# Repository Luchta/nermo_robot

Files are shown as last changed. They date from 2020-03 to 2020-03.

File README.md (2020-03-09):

# nermo_robot
 Hardware repository with all necessary files to build the NeRmo robot.

## DISCLAIMER

 This submission is to be used within the general terms of service of the Human Brain Project (HBP). In particular, users should not download the following code if they intend to make a military use of it.

## Repository Structure
* 3D Printing
	* STL_Files
	* Parts List
* Electronics
	* Eagle Files
	* Parts List
* Nermo User Manual.pdf
* README.md
* LICENSE

## License
[GPLv3](https://fsf.org/)

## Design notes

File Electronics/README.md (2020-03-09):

# nermo_robot
 Electronics Subfolder

## Custom PCBs

* LegSensorBoard
* RPiZWAdapterBoard
* ServoBoard
* Wire_Distr

## License
[GPLv3](https://fsf.org/)

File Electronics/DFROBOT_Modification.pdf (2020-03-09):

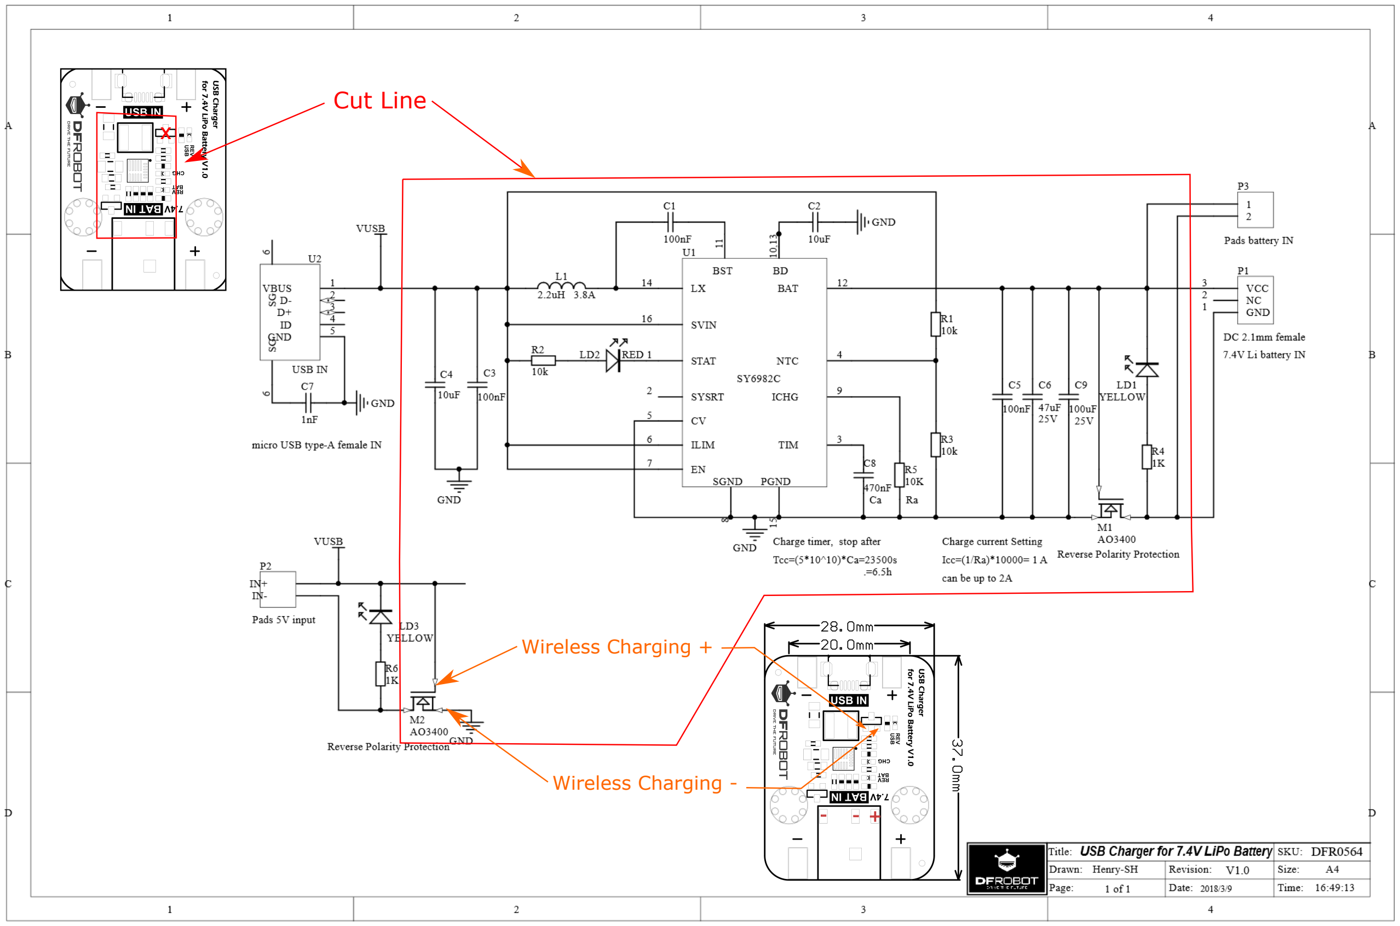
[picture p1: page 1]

### Cut Line

Wireless Charging +

Wireless Charging -

X

- - +

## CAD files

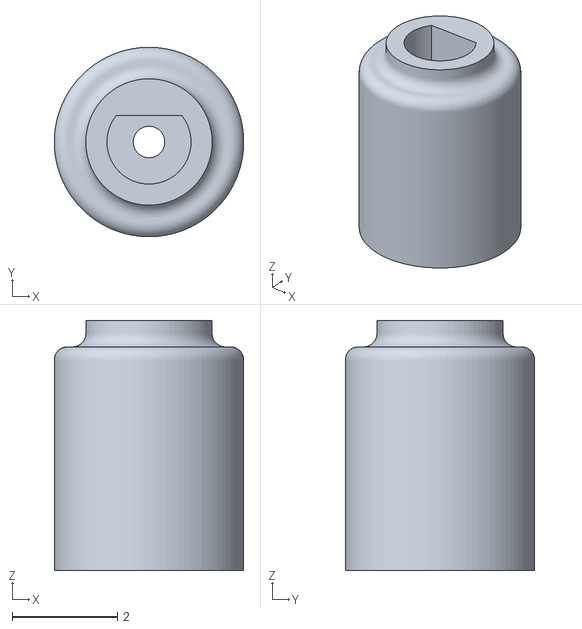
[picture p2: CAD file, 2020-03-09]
3D_Printing/Magnet_holder.stl
3.60 x 3.60 x 4.75

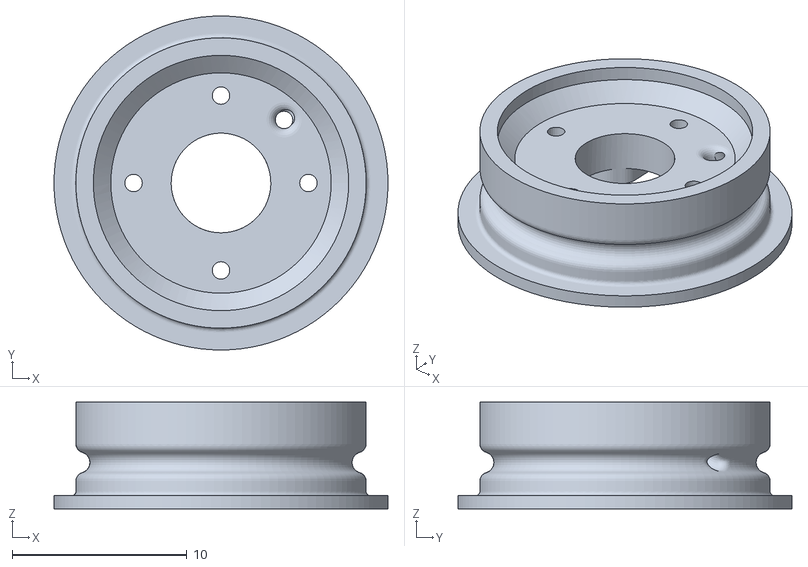
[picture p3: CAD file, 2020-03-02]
3D_Printing/Leg_Coil.stl
19.1 x 19.1 x 6.10

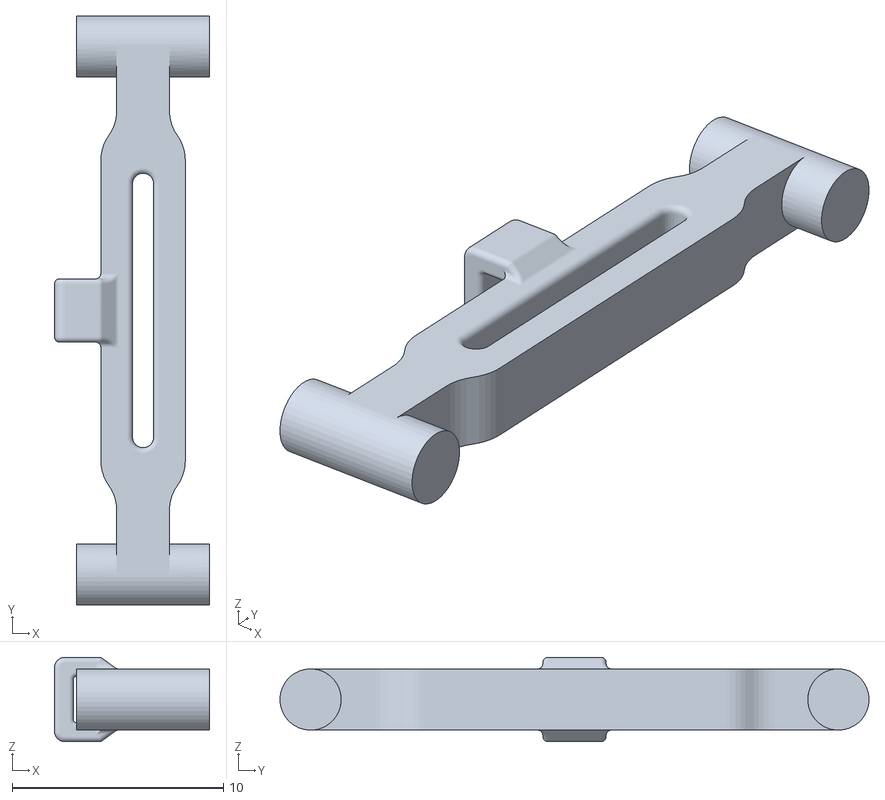
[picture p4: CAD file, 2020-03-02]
3D_Printing/Leg_Hind_Linkage.stl
7.35 x 27.9 x 4.00

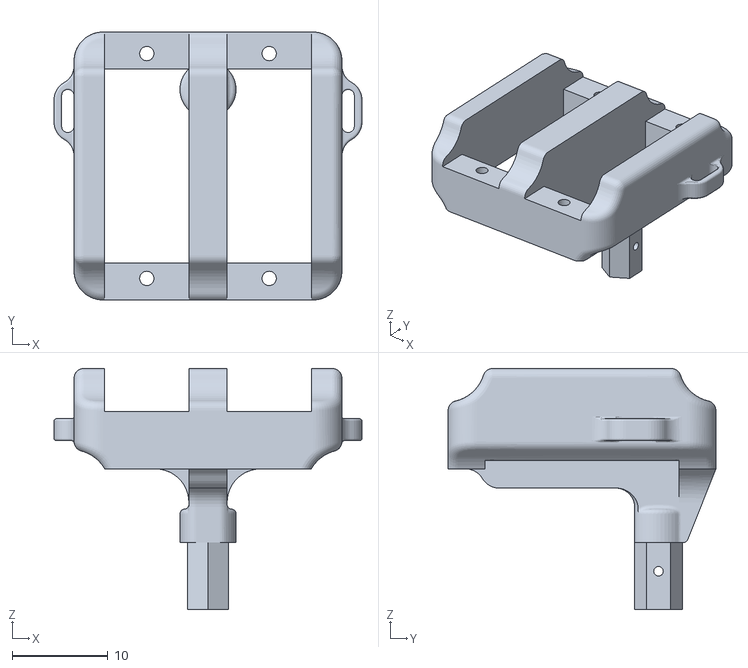
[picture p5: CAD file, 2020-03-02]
3D_Printing/Hip.stl
32.2 x 28.0 x 25.2

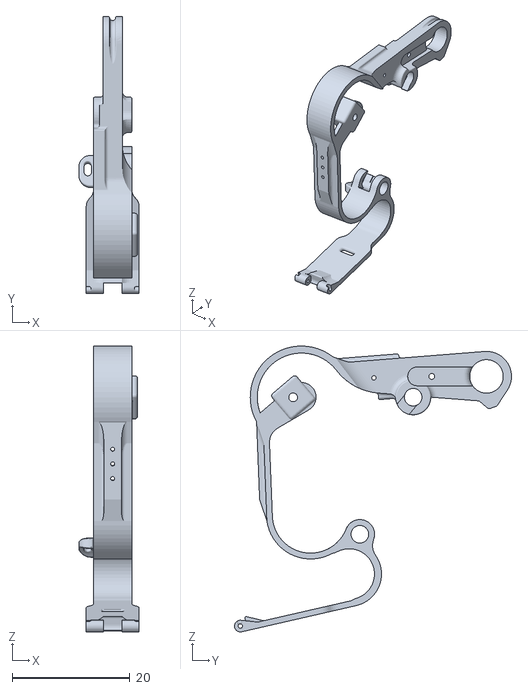
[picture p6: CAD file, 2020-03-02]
3D_Printing/Leg_Hind_Left.stl
10.2 x 47.1 x 48.6

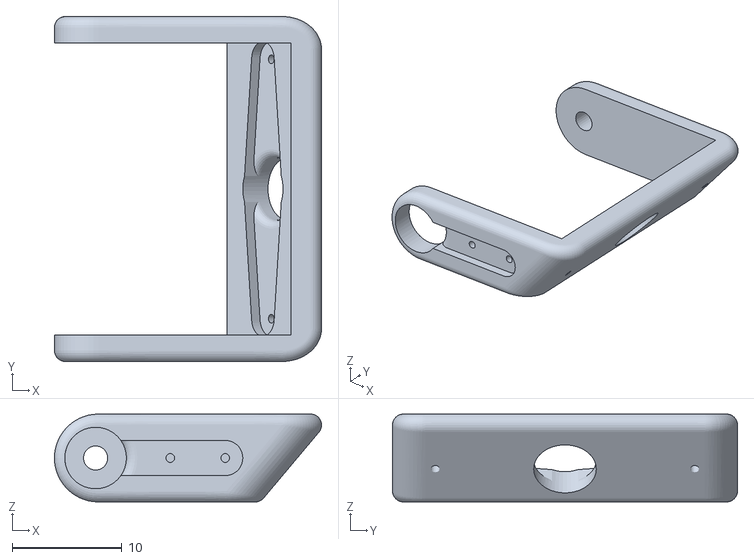
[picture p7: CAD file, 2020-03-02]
3D_Printing/Head_Neck.stl
24.3 x 31.4 x 8.00

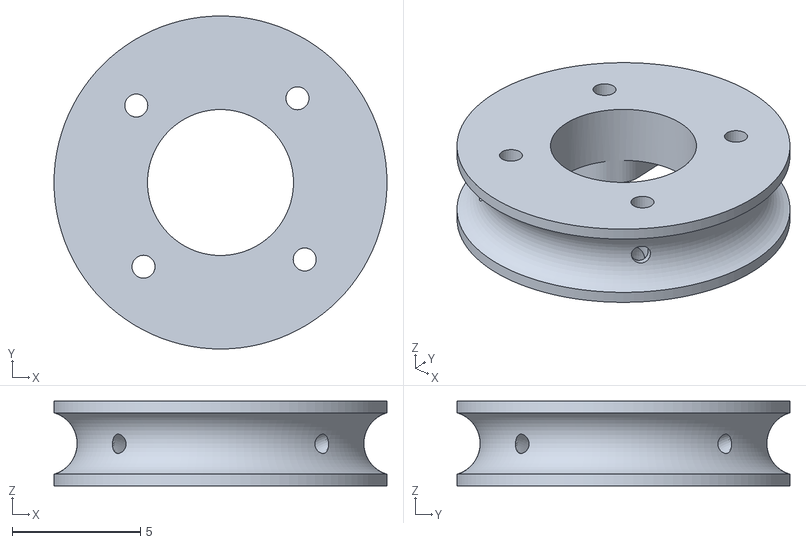
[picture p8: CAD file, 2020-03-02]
3D_Printing/Body_Coil.stl
13.0 x 13.0 x 3.30

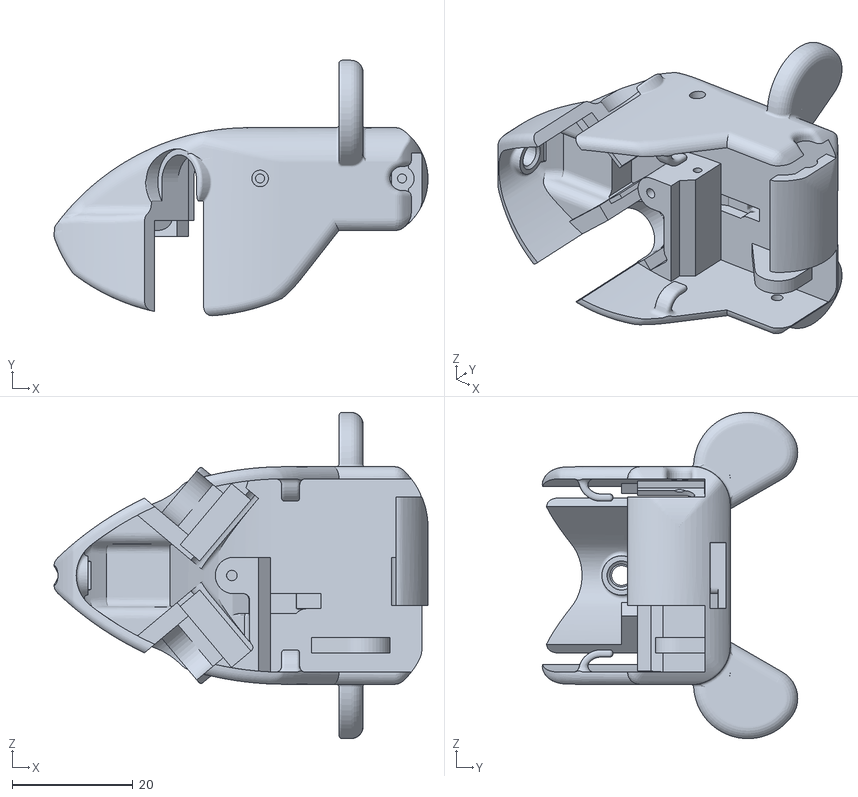
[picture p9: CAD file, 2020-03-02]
3D_Printing/Head.stl
61.9 x 42.3 x 54.0

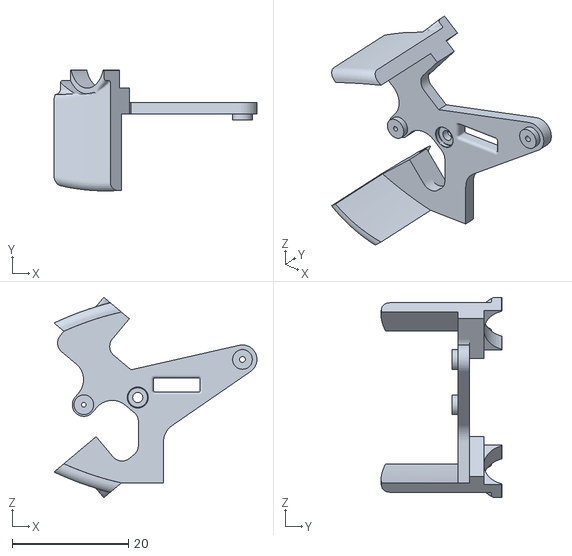
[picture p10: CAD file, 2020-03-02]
3D_Printing/Head_Camera_mount.stl
34.9 x 20.8 x 34.5

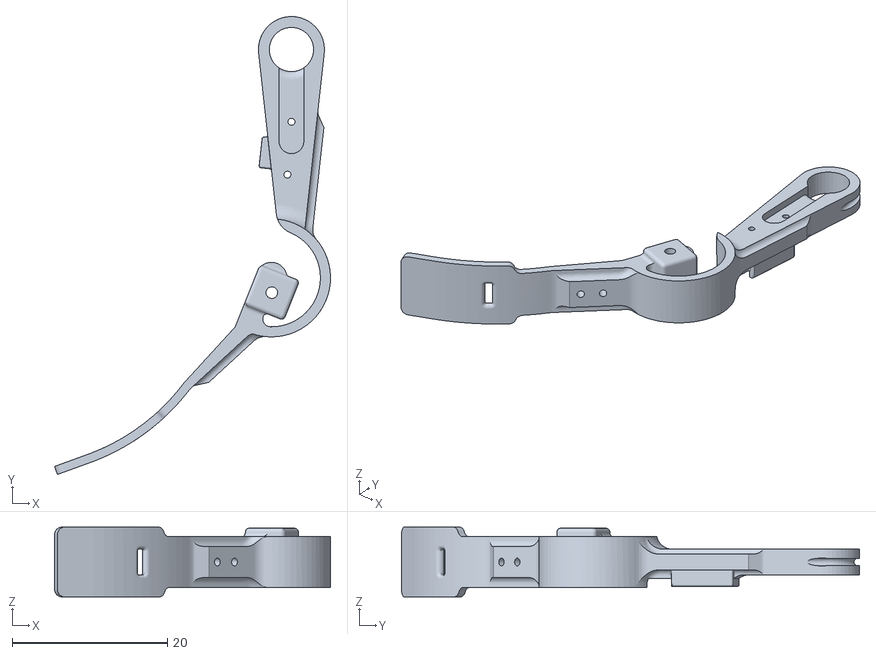
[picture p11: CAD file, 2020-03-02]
3D_Printing/Leg_Fore_Left.stl
35.5 x 58.9 x 9.00

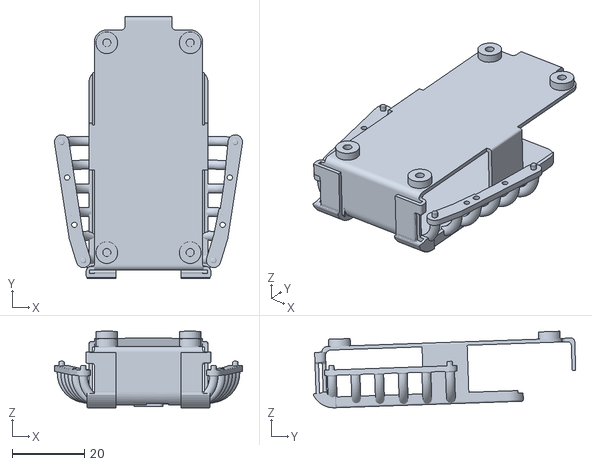
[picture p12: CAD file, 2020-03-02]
3D_Printing/Body_Solarplexus.stl
52.0 x 72.6 x 21.2

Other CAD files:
3D_Printing/Leg_Hind_Right.stl
3D_Printing/Leg_Fore_Right.stl

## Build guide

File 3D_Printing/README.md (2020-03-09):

# nermo_robot
 Hardware Subfolder
 
 All parts will have to be printed using Selective Laser Sintering (SLS) with Nylon (eos PA 2200 or similar).

## STLs to be 3D Printed

* Body
	* Body Coil (2 pcs)
	* Body Solarplexus (1 pcs)
	* Tail (1 pcs)
* Head
	* Head (1 pcs)
	* Head Camera mount (1 pcs)
	* Head Neck (1 pcs)
* Legs
	* Hip (4 pcs)
	* Leg Coil (4 pcs)
	* Leg Fore Left (1 pcs)
	* Leg Fore Right (1 pcs)
	* Leg Hind Left (1 pcs)
	* Leg Hind Right (1 pcs)
	* Leg Hind Linkage (2 pcs)
*Servos
	* Magnet_holder

## License
[GPLv3](https://fsf.org/)

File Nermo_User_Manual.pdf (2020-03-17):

# Nermo Robot

# User Manual

## Peer Lucas

### This Manual and the Robot resources are available free of charge from: https://github.com/Luchta/nermo robot (Hardware) https://github.com/Luchta/nermo code (Code) https://github.com/Luchta/nermo simulation (Simulation)

Abstract

### This manual serves to build, assamble and use the final version of the Neurorobotic mouse

robot, also called Nermo. This biomimetic robot is modular and low-cost; it was created to mimic the locomotion of a rodents, and has the size of a common rat (Rattus Norvegicus). The robot is untethered, easy to use and simple to produce; it thus can be used as a universal research platform. It is based on tendon-driven actuation, which enables the implementation of a compliant leg and body design and thus enables adaptive and dynamic walking motions. Small biomimetic robots can be useful for behavioural/social studies in combination with animals, or for investigating new, efficient types of locomotion for exploration systems. Combined with digital twins, they are a useful tool to reduce the reality gap between simulation and the real world.

Key words

Rodent; mouse; rat; robot; locomotion; biomimetic; tendon-driven actuation; Nermo.

i

# Table of Contents

1 Introduction | 1
2 Parts List | | 2
2.1 Custom Parts and Reusables | 3
3 Preparations | 4
3.1 Electronics | 4
3.1.1 | Servos | 4
3.1.2 | Spine Adapter Board | 4
3.1.3 | Leg Sensor Board | 5
3.1.4 | USB Hub | 5
3.1.5 | Wire Harness | 6
3.2 Reworking printing parts | 7
3.3 Coils | | 8
4 Components Assembly | 9
4.1 Hindleg | 10
4.2 Hindleg Module | 11
4.3 Foreleg | | 11
4.4 Foreleg Module | 12
4.5 Soldering Leg Modules | 12
4.6 Body Module | 13
4.7 Power and Compute Module | 14
4.8 Tail | | 16
4.9 Head | | 17
5 Whole Robot Assembly | 19
5.1 Stringing | 20
5.1.1 | Foreleg | 20
5.1.2 | Hindleg | 20
5.1.3 | Body Module | 21
5.1.4 | Tail Module | 22
5.2 Centre-line Assembly | 22
5.3 Wiring | | 23
6 First Setup | | 25
6.1 Connection Protocols | 25
6.2 Servo Programming | 25
6.3 Raspberry Pi setup | 26
6.4 Control software setup | 26
6.5 Leg setup | 26
7 Usage | | 27
7.1 Overview | 27
7.2 Charging | 27
7.3 Communication | 28
7.4 Control | | 29
References | | 30

ii

# List of Tables

Table 1 List of parts for the 13 modified servos. | 3

### Table 2 All additional parts needed from the original PowerHD HD-DSM44 Servo pack-

ages. | 3
Table 3 WIFI setup for the robot | 25
Table 4 Connection settings for the UART connections. | 25
Table 5 Servo IDs on the robot. | 28

# List of Figures

Fig. 1 Assembly of the custom Servos | 4
Fig. 2 Spine assembly board with all regulator and adapter boards. | 4
Fig. 3 Leg and pressure sensor prepared with wire. | 5
Fig. 4 Disassembly of the USB Hub. | 5
Fig. 5 Assembly of the USB Hub with the cameras. | 5
Fig. 6 Wire harness for connecting the 13 servos to the Spine Adapter Board. | 6

### Fig. 7 Detail view of the wire pathways in the body of the robot in red. The pathways

are symmetrical. Top: transparent body, Bottom: Solid body | 7

### Fig. 8 Detail view of the wire pathways in the tail of the robot in red. The pathways are

symmetrical. Top: transparent body, Bottom: Solid body | 7
Fig. 9 Assembly of the tendon coils. Top: Body coil, Bottom: Leg coil | 8
Fig. 10 NeRmo Module tree. | 9
Fig. 11 Exploded view of the Robot, without the left foreleg. | 9
Fig. 12 Assembly Process for the Hindlegs. | 10
Fig. 13 Soldering of the leg modules with schematic. | 12
Fig. 14 Assembly of the Body module. | 13
Fig. 15 Assembled Body module with transparent Body. | 13
Fig. 16 Assembly of the charging coil to the Power and Compute Module. | 14
Fig. 17 Assembly of the Power and Compute Module. | 15
Fig. 18 Connection of the charging board and the Spine Adapter board. | 15
Fig. 19 Assembly of the Tail Module | 16
Fig. 20 Head Module components | 17
Fig. 21 Assembly and schematic of the Head Sensors. | 18
Fig. 22 Assembly of the Head steps A-E. | 18
Fig. 23 Assembly of all sub modules to the complete Nermo Robot. | 19
Fig. 24 Stringing of the foreleg. | 20
Fig. 25 Stringing of the hindleg. | 20
Fig. 26 Stringing of the lateral tendon on the body module. | 21
Fig. 27 Stringing of the flex tendon on top of the body module. | 21
Fig. 28 Stringing of the foreleg. | 22
Fig. 29 Assembly of the centre line of the robot. | 22
Fig. 30 Attaching the Wiring harness to the leg modules | 23
Fig. 31 Attached Wire harnesses to the Spine, and both Leg sides. | 23
Fig. 32 Power and compute module connectors. | 24

### Fig. 33 Power and compute module attached to the body module with connected usb plug. 24

Fig. 34 programming cable to connect to the servos. | 25

### iii

Fig. 35 Initial setup position of the robot. | 26
Fig. 36 Electrical setup of the robot. | 27
Fig. 37 charging coil of the robot. | 28

iv

### 1. Introduction

The present report details the evolution of the so-called Neurorobotic Mouse robot, and presents the main features of its latest release. The development of that robot was initiated in 2018 [1] with the view to become a general-purpose research robot for roboticists and neuroscientists alike. Over the last two years, four main successive versions [2] were built before finally ob-taining the final version described herein. The minimal set of features for such a robot to be

### useful to all intended users [2] are:

- Flexible and functional backbones.
- Biologically relevant limbs with a small number of parts (for ease for build).
- A functional tail (for facilitating balance and locomotion).

### - A sensory system sufficient to provide the robot with capabilities for autonomous navi-

gation and decision-making.

- Tendon-driven actuation that mimics the biological musculoskeletal system of a rodent.

Additionally, the perquisites for this project where to create a low-cost and modular robot, in order to facilitate uptake of the device in the research community. These features were already realized with the last version of this robot [2]. The Final version presented herein features multiple improvements over previous iterations, especially ease of assembly and robustness to allow for a wider user group. Additionally, we created a digital twin of the robot (i.e. a simulated model, reproducing the characteristics of the real one with as much fidelity as possible) within the Neurorobotics Platform (NRP).

### 2. Parts List

Category | Item | Description | Quantity
Electronics
| Raspberry Pi Zero W | Main Computer | 1
| Micro SD memory card | Storage for RasPi | 1
| Akku-Pack, Li-Polymer, 7,4 V
| 1000 mAh, 2, 25 C | Battery | 1
| Nose Touch Button | Nose Touch Button | 1
| 1.0mm 1.0 SH Micro JST
| with 15cm Wire | Cable to connect Servos | 17
| Cable to connect leg sensor PCB | Cable to connect leg sensor
| | PCB | 4
| 0-200g Thin Film Pressure Sensor | Foot Pressure Sensor | 4
| Micro USB Hub | USB Hub for Cameras | 1
| U1-MWD | Camera in Head | 2
| Modified PowerHD HD-DSM44 | Motors | 13
| Spine Adapter Board | Power and Motor control | 2
| Leg Sensor Board | Angle and Pressure sensor | 2
| 4 Hole Wiring Board | Wiring Harness | 2
| 5 Hole Wiring Board | Wiring Harness | 1
Mechanics
| M2x8 | Head Tilt Axis | 1
| M2x6 | Camera holder | 1
| M2x14 | Tail Mount | 1
| M2 Stop-nut | Tail Mount | 1
| M1x4 | Leg-Wire Fixes | 20
| M1*3 | Leg-Wire Fixes | 10
| M1x8 | Hip Fix | 8
| Magnet 4x4x4 mm | Leg Sensor Magnet | 8
| M2,5*6,5 | Distance holder for RasPi | 4
| India rubber tape
| self-adhesive | Feet covering | 1
| Perlon thread
| ø0,3 mm length 50 m | Tendons | 1
3D Prints | | | 22
| Body | Main Body of the Mouse | 1
| Body Coil | Small Coils for Tendons | 2
| Body Solarplexus | Holder for Battery and Raspi | 1
| Head | Robot Head | 1
| Head Camera mount | mount for all head components | 1
| Head Neck | Connection Head-Body | 1
| Hip | Servo Mount for all Legs | 4
| Leg Coil | Coils for Leg tendons | 4
| Leg Fore Left | Left Foreleg | 1
| Leg Fore Right | Right Foreleg | 1
| Leg Hind Left | Left Hindleg | 1
| Leg Hind Right | Right Hindleg | 1
| Leg Hind Linkage | Linkage for Hindlegs | 2
| Tail | Tail | 1

### 2.1 Custom Parts and Reusables

The Servo motors for this robot will have to be modified according to the servo modification manual in this repository. The parts needed for the modification are the following Table 1.

Item | Description | Quantity
PowerHD HD-DSM44 | Servo | 13
M1x12 | Attach servo PCB | 26
Custom servo PCB | New control board | 13
Magnet 2x2x2 mm | Magnet for Hall sensor | 13
Servo magnet holder | 3D printed magnet holder | 13

Table 1. List of parts for the 13 modified servos.

Additionally. some parts come with the original PowerHD HD-DSM44 servos, that will be used in the build as listed in Table 2.

Item | Description | Quantity
Servo Horn Cross | All Coils | 6
Servo Horn Lever | Legs and Neck | 5
Servo Horn Bar | Neck and Tail | 2
Servo Horn Screw | Mount all Horns 1.6x3 | 13
Attachment Screw | Mount all Servos wood screw 1.6x6 (DIN 7981) | 26

Table 2. All additional parts needed from the original PowerHD HD-DSM44 Servo packages.

### 3. Preparations

There are some preparations to be taken before the robot can be assembled.

### 3.1 Electronics

Additionally to the Servo PCBs there are two types of PCBs that will have to be assembled before the robot can be build. Those are the Spine Adapter Board and the Leg Sensor Board. For both boards the eagle files and assembly manuals can be found in the folder ”/Electronics/Eagle/”

### 3.1.1 Servos

Before starting with the Robot’s assembly, make sure that you have 13 assembled servos. The Manual on how to assemble the custom servos can be found in the same directory as this manual (Servo Assembly.pdf) Figure 1 shows a overview of the assembly process.

Fig. 1. Assembly of the custom Servos

### 3.1.2 Spine Adapter Board

The Spine Adapter board goes on top of the Raspberry Pi Zero and handles communication and power distribution in the robot. Additionally to the PCB there are some off the shelf parts, that are added to the board as shown in Figure 2.

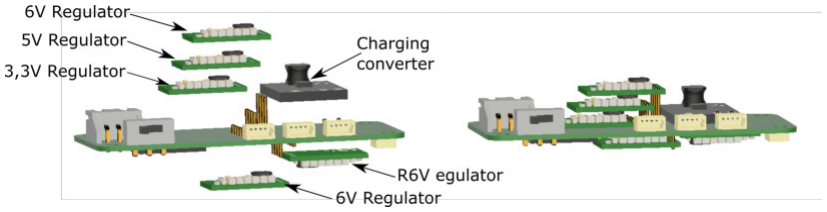
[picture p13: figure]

Fig. 2. Spine assembly board with all regulator and adapter boards.

### 3.1.3 Leg Sensor Board

The leg sensor boards have a hall sensor to measure the knee/elbow angles as well as a ADC to measure the ground pressure with the pressure sensors. To have less work later on you can solder wires already to the according pads (Figure 3).

Fig. 3. Leg and pressure sensor prepared with wire.

### 3.1.4 USB Hub

To address the cameras in the Head, we used a simple USB-Hub. This Hub can be bought from Amazon or anywhere else. We only need the core pcb as shown in Figure 4. After Disassembly, the cameras and a USB cable can be soldered to the USB Hub as shown in Figure 5.

Fig. 4. Disassembly of the USB Hub.

Fig. 5. Assembly of the USB Hub with the cameras.

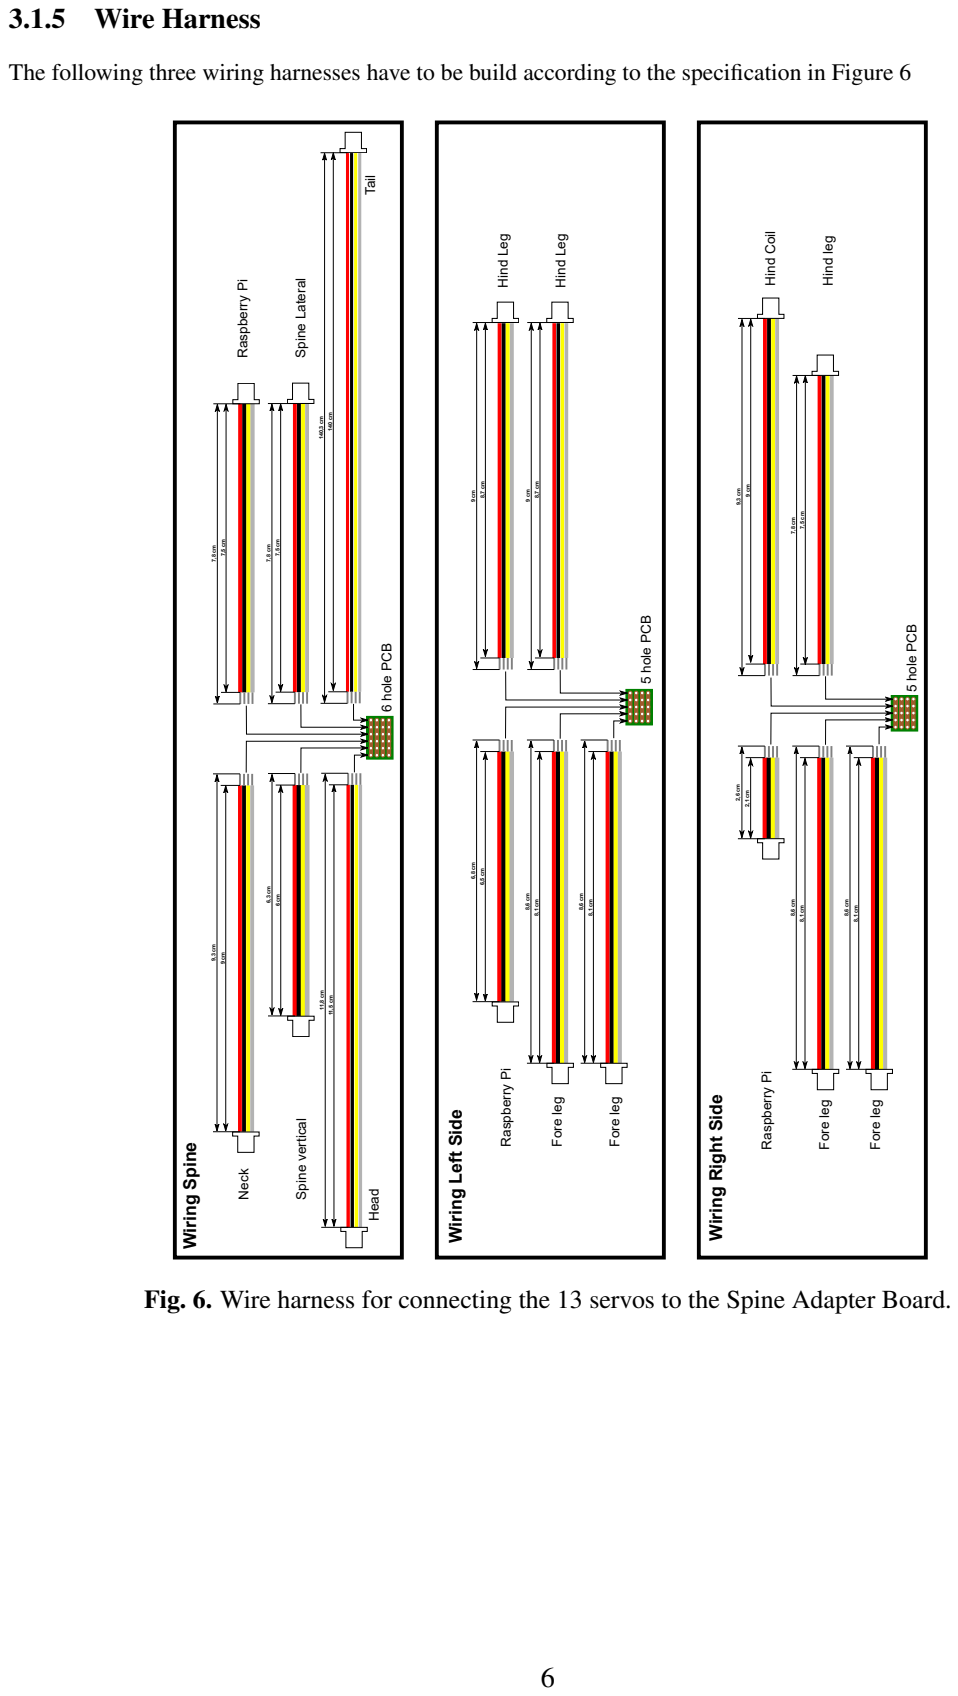
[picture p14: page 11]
3.1.5 Wire Harness; Raspberry Pi; Fore leg; Hind Coil; Hind leg; Hind Leg; Spine Lateral; Tail Head; Neck; Spine vertical; Wiring Spine; 6 hole PCB; 5 hole PCB

The following three wiring harnesses have to be build according to the specification in Figure 6

Wiring Right Side

Wiring Left Side

Fig. 6. Wire harness for connecting the 13 servos to the Spine Adapter Board.

### 3.2 Reworking printing parts

In order to be able to insert the wires to actuate the spine and tail, you will have to ensure, that the pathways are clear. The pathways are usually blocked slightly by residue of the Nylon powder used for 3D printing. This is most easily achieved by pushing a wire or a needle through the entire length of the respective pathway.
There are 5 Pathways to be cleared, three in the Body of the robot (Figure 7) and two in the Tail (Figure 8).

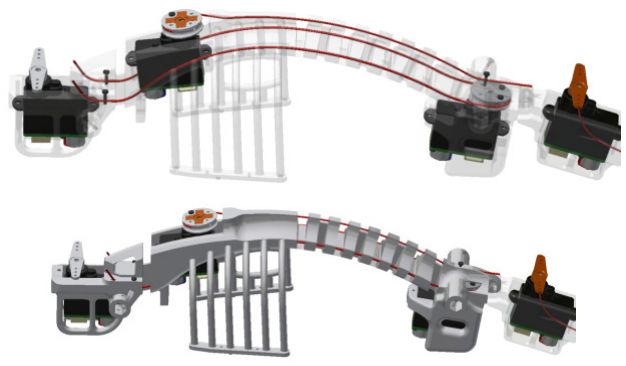
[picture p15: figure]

Fig. 7. Detail view of the wire pathways in the body of the robot in red. The pathways are symmetrical. Top: transparent body, Bottom: Solid body

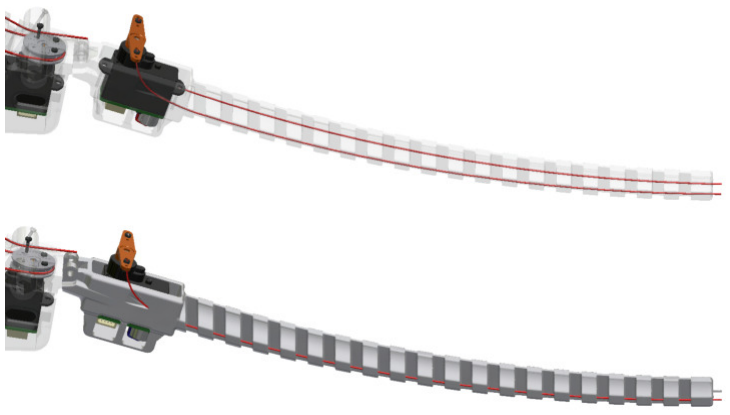
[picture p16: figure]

Fig. 8. Detail view of the wire pathways in the tail of the robot in red. The pathways are symmetrical. Top: transparent body, Bottom: Solid body

### 3.3 Coils

To attach the tendon coils to the servos, servo horns have to be attached to the 3D printed parts. This is best achieved by using Super glue, please ensure that the servo horns are fitted fully into the coils.

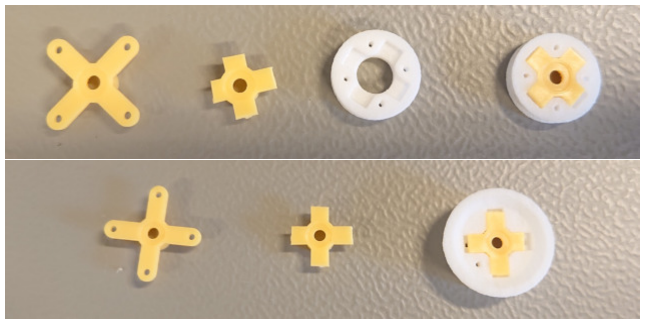
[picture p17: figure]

Fig. 9. Assembly of the tendon coils. Top: Body coil, Bottom: Leg coil

### 4. Components Assembly

The Robot can be separated into multiple Modules as shown in Figure 10. These modules will be assembled each on their own, until the full robot can be completed.

Fig. 10. NeRmo Module tree.

The modules can be seen in Figure 11 labelled on the actual Robot.

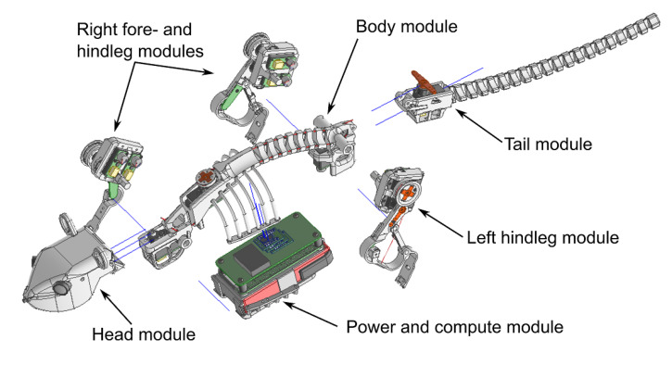
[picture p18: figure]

Fig. 11. Exploded view of the Robot, without the left foreleg.

For this manual, we will start with the Leg modules and work ourselves on to the full robot.

### 4.1 Hindleg

Needed Parts:
Item | Quantity
Leg Hind Left/Right (3D-Print) Leg Hind Linkage (3D-Print) M1x4 (Screw) Servo Horn (Servo Parts) Leg Sensor PCB with Wire Pressure Sensor PCB with Wire 4x4x4 mm Magnet small piece rubber tape | 1 1 2 1 1 1 1 1

The process is the same for the left and the right Hindleg. All mounting holes are included in the 3D print, you might have to clean up the holes but you will not need to drill new holes for mounting. If you drill new holes you are placing the component wrong.

A First screw the Servo Horn in place.

B Push the Magnet into the provided Space in the Knee. WARNING! Make sure, that the separation line of the magnet poles is as indicated on the picture or the sensor will not work.

C Screw the Leg Sensor in the provided place on the other side of the Leg. Make sure that the Hall sensor is facing the Magnet.

C,D Thread the Pressure sensor cables through the hole in the foot (1), the guide on the ankle (2) and the guide on the Linkage (3) up to the Leg Sensor.

E Solder the pressure Sensor to the Leg sensor and add the rubber tape to the sole of the Foot.

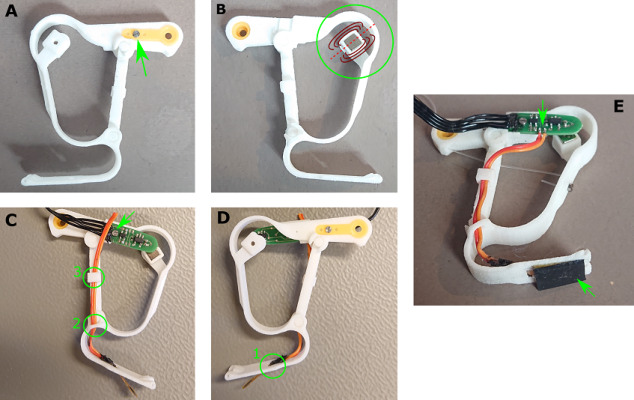
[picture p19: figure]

Fig. 12. Assembly Process for the Hindlegs.

### 4.2 Hindleg Module

The Hindleg Module combines the Hindleg with the Hip, the Servos and the Coil for the Leg Tendon. The Stringing of the Tendons itself will be handled in its own section later on.

Needed Parts:
Item | Quantity
Hindleg Left/Right Hip (3D-Print) Leg Coil (3D-Print) Servo Horn Cross (Servo Parts) Servos (ID 0) Servos (ID 1) Servo mount screws (Servo Parts) | 1 1 1 1 1 1 4

### 4.3 Foreleg

Needed Parts:
Item | Quantity
Leg Fore Left/Right (3D-Print) M1x4 (Screw) Servo Horn (Servo Parts) Leg Sensor PCB with Wire Pressure Sensor PCB with Wire 4x4x4 mm Magnet small piece rubber tape | 1 2 1 1 1 1 1

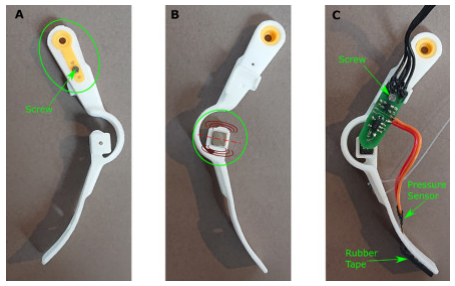
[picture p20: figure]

The process is the same for the left and the right Foreleg. All mounting holes are included in the 3D print, you might have to clean up the holes but you will not need to drill new holes for mounting. If you drill new holes you are placing the component wrong.

- A First screw the Servo Horn in place.
- B Push the Magnet into the provided Space in the Knee. WARNING! Make sure, that the separation line of the magnet poles is as indicated on the picture or the sensor will not work.
- C Screw the Leg Sensor in the provided place on the other side of the Leg. Make sure that the Hall sensor is facing the Magnet.
- C Thread the Pressure sensor cables through the hole in the foot.
- C Solder the pressure Sensor to the Leg sensor and add the rubber tape to the sole of the Foot.

### 4.4 Foreleg Module

The Foreleg Module combines the Foreleg with the Hip, the Servos and the Coil for the Leg Tendon. The Stringing of the Tendons itself will be handled in its own section later on.

Needed Parts:
Item | Quantity
Foreleg Left/Right Hip (3D-Print) Leg Coil (3D-Print) Servos (ID 2) Servos (ID 3) Servo-horn Cross (Servo Parts) Servo mount screws (Servo Parts) | 1 1 1 1 1 1 4

### 4.5 Soldering Leg Modules

The lead wires to the leg sensor board of all leg modules have to be soldered to the servo, closest to the leg. The schematic and the resulting connection is shown in Figure 13. Make sure to thread the cables through the guide on the hip to avoid any stress on the soldering connections during motions. You can also fix the cables to the PCBs with silicon or glue.

Fig. 13. Soldering of the leg modules with schematic.

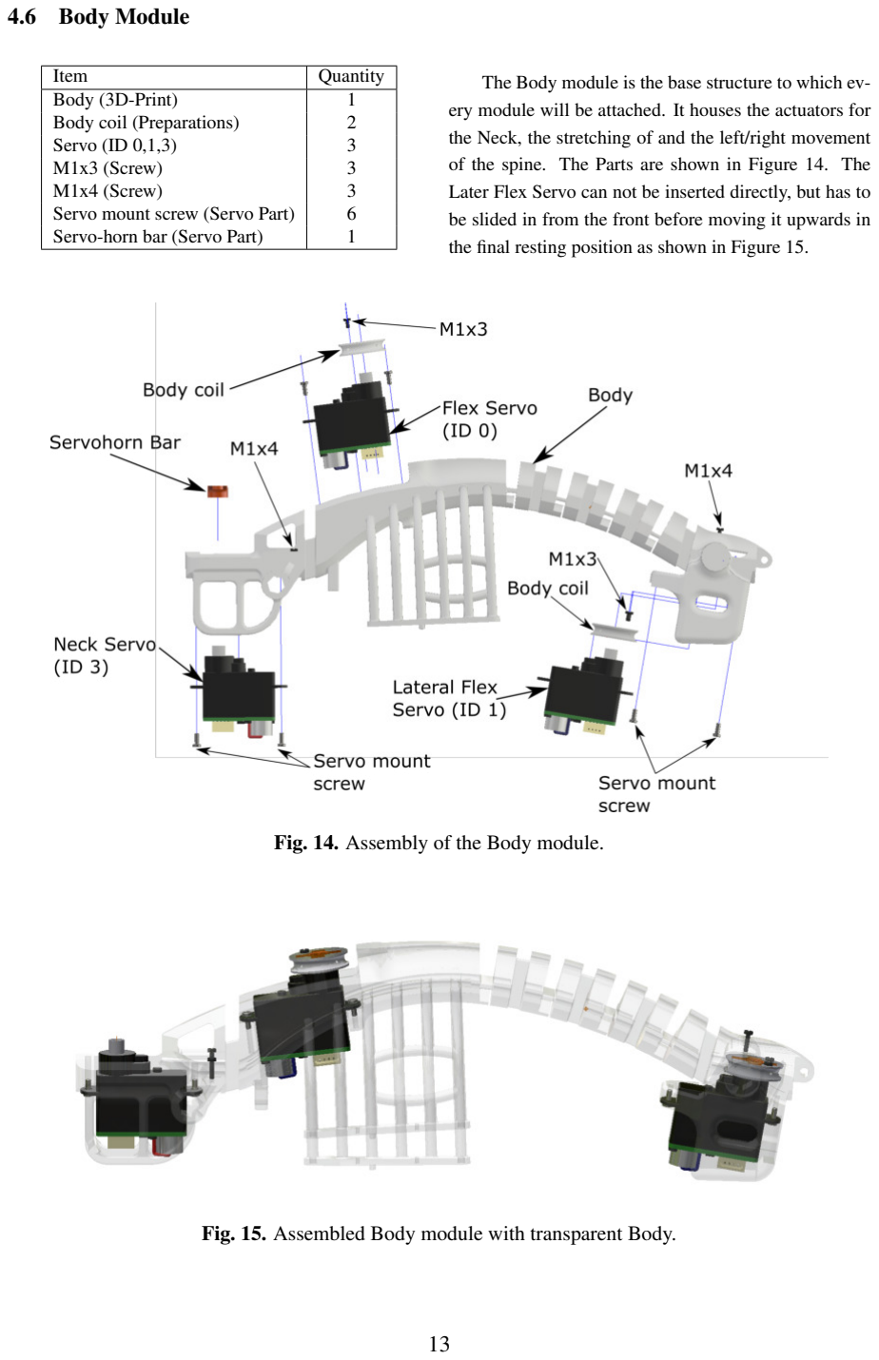
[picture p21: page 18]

### 4.6 Body Module

Item | Quantity
Body (3D-Print) Body coil (Preparations) Servo (ID 0,1,3) M1x3 (Screw) M1x4 (Screw) Servo mount screw (Servo Part) Servo-horn bar (Servo Part) | 1 2 3 3 3 6 1

The Body module is the base structure to which ev-ery module will be attached. It houses the actuators for the Neck, the stretching of and the left/right movement of the spine. The Parts are shown in Figure 14. The Later Flex Servo can not be inserted directly, but has to be slided in from the front before moving it upwards in the final resting position as shown in Figure 15.

Fig. 14. Assembly of the Body module.

Fig. 15. Assembled Body module with transparent Body.

### 4.7 Power and Compute Module

Item | Quantity
Body Solarplexus (3D-Print) Spine Adapter board Raspberry Pi Zero WH M2.5x4 (Screw) M2.5x6.5 Distancer 1000 mAh 7.4 V Battery Wireless charging coil Epoxy glue | 1 1 1 4 4 1 1 1

If you want to have the wireless charging feature for the robot, you will have to attach the charging coil to the Solarplexus as shown in Figure 16. First insert the Charging Board into the slot at the front of the Solarplexus (A), then you can bend the coil on to fit into the bottom of the Solarplexus and glue it in place with the Epoxy (B). Finally add the Protective shield that comes with the charger into the battery compartment.

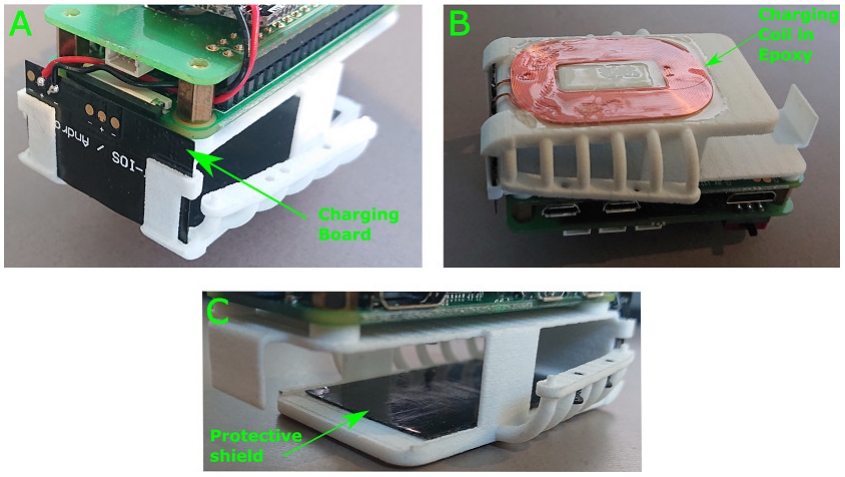
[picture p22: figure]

Fig. 16. Assembly of the charging coil to the Power and Compute Module.

Then you can attach the Raspberry Pi and the Spine Adapter board on top of the Solarplexus using the dis-tancers and the screws as shown in Figure 17. Finally to attach the charger to the Spine adapter board, solder a wire from the charging board to the converter board on the Spine Adapter board as shown in Figure 18.

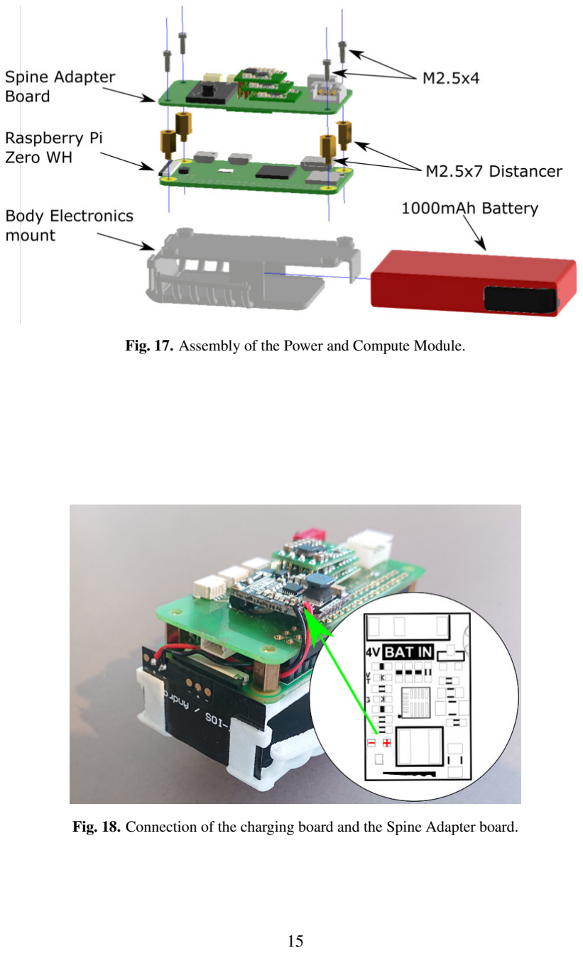
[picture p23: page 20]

Fig. 17. Assembly of the Power and Compute Module.

Fig. 18. Connection of the charging board and the Spine Adapter board.

### 4.8 Tail

Item | Quantity
Tail (3D-Print) Servo (ID 2) M1x3 (Screw) M1x2 (Screw) Servo mount screw (Servo Part) Servo-horn screw (Servo Part) | 1 1 2 2 2 1

For the tail, only one motor has to be attached in the according cage, including the servo horn and some screws needed for stringing later on, see Figure 19. The Stringing of the Tendons itself will be handled in its own section later on.

Fig. 19. Assembly of the Tail Module

### 4.9 Head

Item | Quantity
Head (3D-Print) Head Neck (3D-Print) Head C mount (3D-Print) Camera USB Hub Nose Button (39-138 BLK) Touch Sensor (TTP223) Servo (ID 4) Servo mount screw (Servo Part) Servo-horn (Servo Part) Servo-horn Bar (Servo Part) Servo-horn screw (Servo Part) M1x3 M1x4 M2x8 M2x6 | 1 1 1 2 1 1 1 1 2 1 1 1 3 2 1 1

The Head is the most complex part of the robot to build. It consists of many parts and needs multiple steps to complete. before building the head, make sure, that you have done the preparations for the USB-cameras and the USB-Hub.

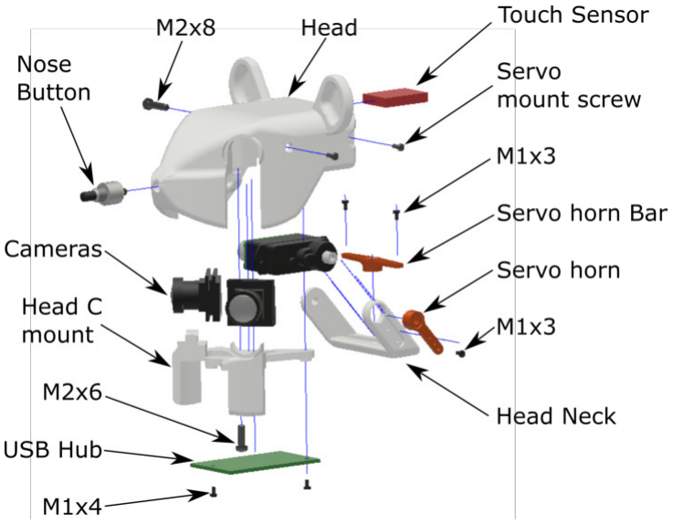
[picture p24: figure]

Fig. 20. Head Module components

The first step is the assembly of the sensors into the head. The schematic is shown in the right of Figure 21. First attach wires to the touch sensor and thread the wires through the cable channel in the top of the head, while pushing the sensor in its compartment. Then you can screw the nose button into the respective place in the head and connect all wires according to the schematic plans. The wire to the Spine Adapter Board should be 13 cm long.
The following Figure 22 shows the remaining step by step assembly of the head module. The steps are as follows:

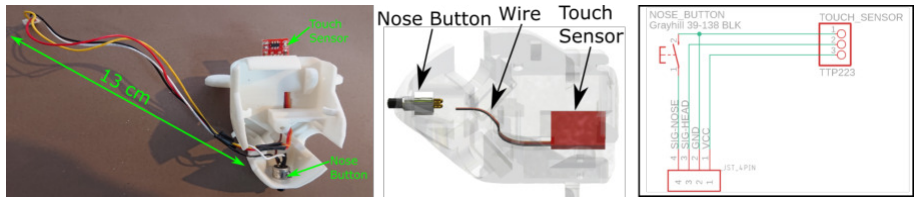
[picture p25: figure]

Fig. 21. Assembly and schematic of the Head Sensors.

A Assemble the Neck with all servo horns as shown in Figure 20 and attach it to the head servo (ID 4). Make sure the motor is set to its centre (0800) position.

B Insert the servo with the neck into the head and secure it with the servo mount screws.

C Insert the two cameras into the two the according recesses. Be careful not to break off the lens from the sensor. The camera with the longer lead wire is the right eye of the head (when facing forward).

D Insert the Head C mount to secure the cameras. Ensure that all camera wires can go unobstructed. And secure it with a M2x6 Screw.

E Attach the USB Hub atop of the Head C mount, make sure, that the camera wires from the right camera are running over the PCB. Then secure it with two M1x3 screws.

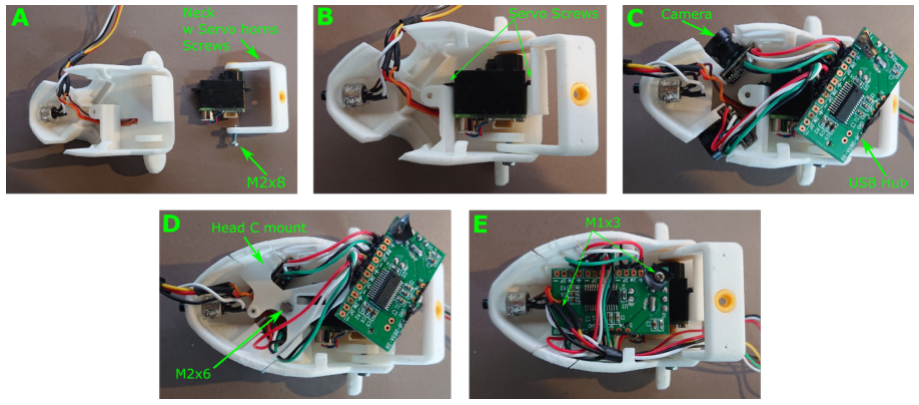
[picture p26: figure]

Fig. 22. Assembly of the Head steps A-E.

### 5. Whole Robot Assembly

Item | Quantity
Body Module Hindleg Module Left Hindleg Module Right Foreleg Module Left Tail Module Power and Compute Module Head Module Wiring Harnesses | 1 1 1 1 1 1 1 3

With all sub modules assembled, we can no start to assemble the complete robot.

Fig. 23. Assembly of all sub modules to the complete Nermo Robot.

### 5.1 Stringing

For inserting the robot tendons, please make sure, that all motors are set to zero, especially the spine motors. For tendons we use nylon wire with a 0,3 mm diameter and a max force of 4 kg. The tendons are fixed with screws, but can be glued into place when the final setup of the robot is completed.

### 5.1.1 Foreleg

To string the foreleg tendon first attach the tendon on the leg as shown in the middle bottom on Figure 24 with a M1x3 screw. Then thread the tendon onto the coil as shown in the figure through the hole in the coil. The tenon can then be tightened fixed with a M1x4 screw.

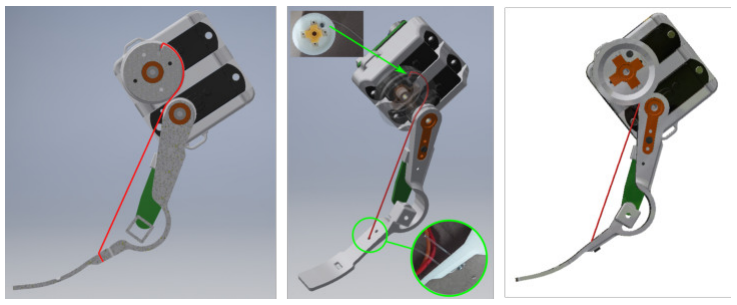
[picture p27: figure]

Fig. 24. Stringing of the foreleg.

### 5.1.2 Hindleg

To string the hindleg tendon first attach the tendon on the shin of the leg as shown in the middle bottom on Figure 25 with a M1x3 screw. Then thread the tendon through the linkage (2) and the hole on the top of the leg (1) and onto the coil as shown in the figure. The tendon can then be tightened through the hole in the coil and fixed with a M1x4 screw.

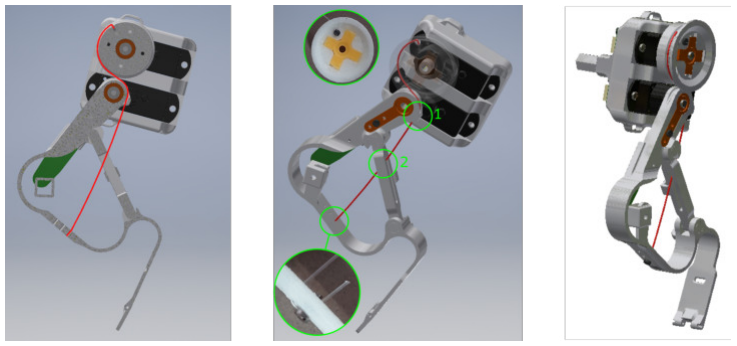
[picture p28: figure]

Fig. 25. Stringing of the hindleg.

### 5.1.3 Body Module

For the left and right lateral tendons prepare two tendons with about 20 cm length and remove the lateral flex servo from the body module. First attach the two tendons on the coil of the lateral flex servo as shown in Figure 26 on the right side. Take care, that the left tendon is attached to the right screw and the right tendon to the left screw to ensure the tendons can moved enough distance later on. The next step is to thread both tendons along their respective pathways until they are at the very front of the body module. You can then reinsert the lateral flex servo into the body module. Finally tighten the strings and fix them at the front with two M1x4 screws.
For the spine flex tendon prepare a 15 cm piece of tendon. Then attach the tendon to the coil at the servo as shown

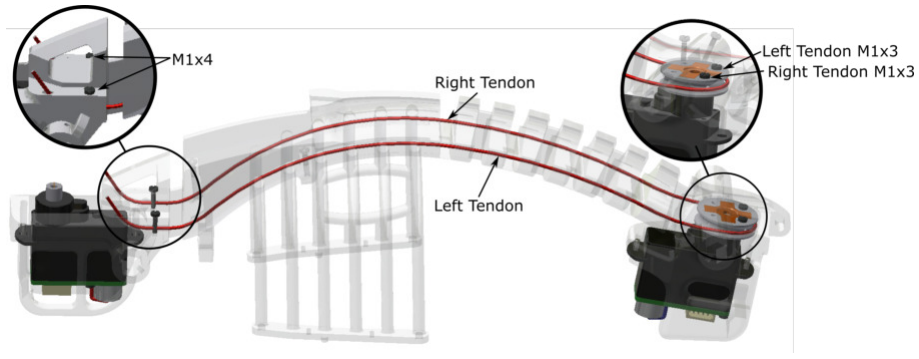
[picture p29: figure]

Fig. 26. Stringing of the lateral tendon on the body module.

in Figure 27. then thread the tendon through to the back of the module, tighten the string and fix it with a M1x4 screw.

Fig. 27. Stringing of the flex tendon on top of the body module.

### 5.1.4 Tail Module

For the tail module prepare two pieces of wire of about 30 cm length. Thread the two pieces through their respective pathways as shown in Figure 28. On the end of the tail, attach the the tendons with two M1x2 screws. On the servo side of the tail, thread the tendons through the holes of the servo horn, tighten the strings and fix them with two M1x3 screws.

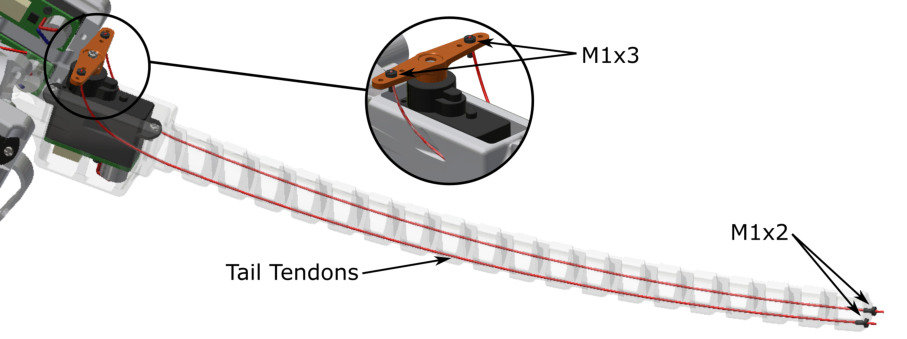
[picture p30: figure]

Fig. 28. Stringing of the foreleg.

### 5.2 Centre-line Assembly

The centre line of the robot consists of the body module together with the tail and the head modules. You will need a M2x11 screw with a Stop-nut and one of the servo horn screws form the servos.

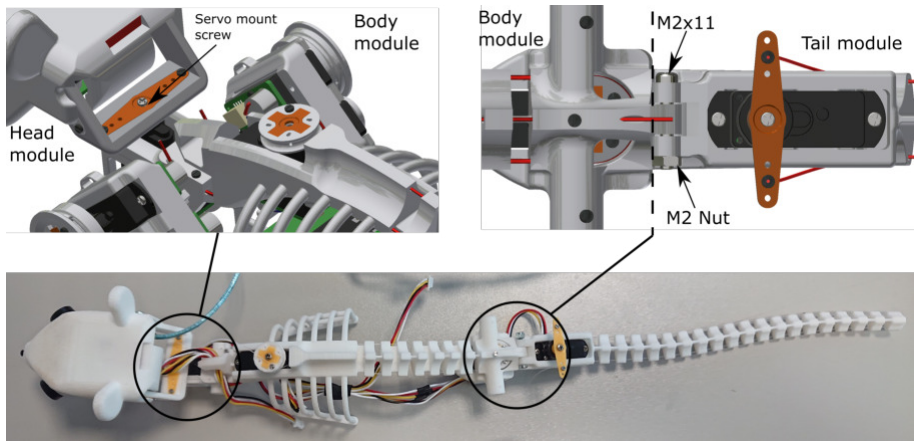
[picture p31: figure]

Fig. 29. Assembly of the centre line of the robot.

### 5.3 Wiring

The Wiring of the servos should be quite clear based on the plan from Figure 6. What is to be taken into account is to remove one of the servos of the leg modules for attaching the wire, as the mounting is in the way of pluging the connector in in the assembled module (Figure 30).
There are 2 places where the central spine wiring will have to be threaded through, at the neck the wiring coming

Fig. 30. Attaching the Wiring harness to the leg modules

from the head can be threaded through the hole in the body module as shown in the enlarged picture in Figure 31. At the tail, the wires can be attached or threaded through at the side of the flex servo.

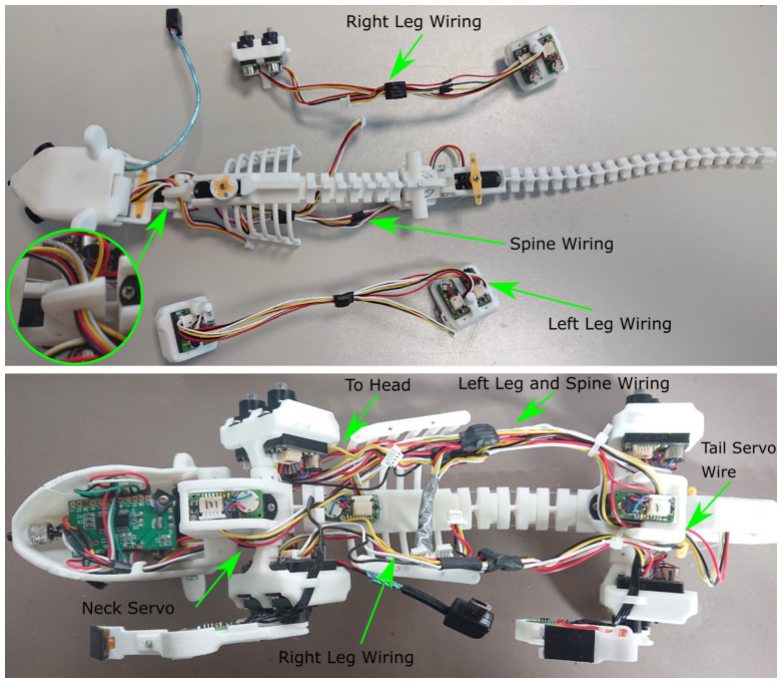
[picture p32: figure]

Fig. 31. Attached Wire harnesses to the Spine, and both Leg sides.

When all three wiring harnesses are attached to the servos you can attach the Leg modules to the body module as shown in Figure 23. The wires are then to be organized as shown in Figure 31.
Finally you can insert the power and compute module. The plugs are to be attached as shown in Figure 32. The module is to be inserted from the bottom as shown in Figure 23. For securing the module to the body four M1x3 screws can be used as shown in Figure 33.

Fig. 32. Power and compute module connectors.

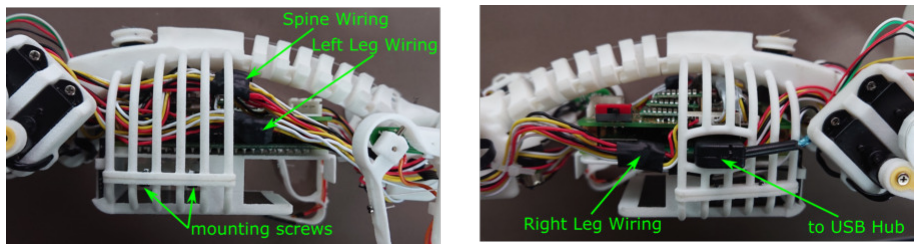
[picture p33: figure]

Fig. 33. Power and compute module attached to the body module with connected usb plug.

### 6. First Setup

Before using the robot, the control environment as well as all joints have to be setup. With building the custom servos and the spine adapter board, you should also have added the newest firmware to those parts. If not, please do so now.

### 6.1 Connection Protocols

When using the pre-installed sd image, the robot is setup to connect to the following wireless network in Table 3.
To connect you can open an ssh connection to the user pi@<IP address> . | The Robot infrastructure uses
SSID | LOSTLITTLEROBOT
Pasword | ********

Table 3. WIFI setup for the robot

mostly single wire UART connections for the servos and normal UART between the Raspberry Pi and the Spine Adapter. The settings for the connection can be taken from Table 4. To connect to the spine or the servos from a computer you can use a UART adapter with TeraTerm or similar software. To program the chips we used the STM32CubeProgrammer.

Connection | Setting | Baud | Setting | Connection
RPI-Spine | Control | 1000000 | 8E1 | UART
Spine-Servo | Control | 1000000 | 8E1 | Single Wire UART
All | Programm | 57600 | 8E1 | UART

Table 4. Connection settings for the UART connections.

### 6.2 Servo Programming

The used programming software is the STM32CubeProgrammer. To connect to the Spine or the Servo you will need a USB to UART adapter. Additionally for the servos, you will need a special wire setup in order to talk via the single wire UART and programm via usual UART, according to the schematics in Figure 34. To set a already

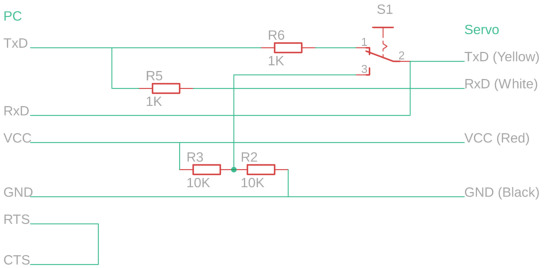
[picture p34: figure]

Fig. 34. programming cable to connect to the servos.

programmed servo into programming mode, connect to the motor and start the bootlaoader mode. Then disconnect the terminal program from the servo (NOT the Cable!) and start the flashing with the CubeProgrammer, same goes for the Spine Adapter. When the servos are connected to the Spine adapter, all servos can be programmed simultaneously by connecting to the spine and selecting the respective mode as explained in subsection 7.4, then again disconnect the terminal software and start the programming.

### 6.3 Raspberry Pi setup

The raspberry Pi runs with raspian, a operating system provided by the Raspberry Pi Foundation. Either you have the already installed the available sd image on an sd card or you can setup the raspi from scratch. For the later please refer to the setup documentation here: https://www.raspberrypi.org/documentation/.

### 6.4 Control software setup

To run the basic control script please clone this repository: https://github.com/Luchta/nermo code and follow the Readme instructions to compile the code. You will have to create a build folder and use ”cmake ..” and ”make” to compile the code. Additionally you can some helper scripts form https://github.com/Luchta/nermo scripts and compile with the same steps as the nermo code repository.

### 6.5 Leg setup

When using the robot for the first time, make sure, that all the legs are in the correct starting positions. The servos on the central line of the robot should all be setup correctly, as the servos have been set to their centre position during assembly. If that has not been done, you will also have to reset the servo horns on those servos. For the legs, first remove all legs and coils from the servos. Then, power on the robot and start the control software. Hit ”i” which sets all motors to an initial position. Then attach the lags as shown in Figure 35, make sure that the left and right side are correctly aligned. Finally make sure, that all joints are aligned as in Figure 35. For the Coils, make sure the strings are tensed without actuating the knee/elbow.

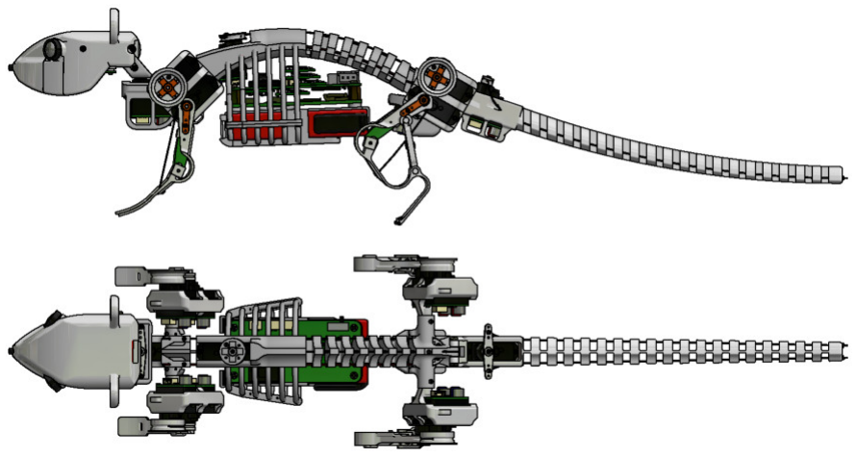
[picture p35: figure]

Fig. 35. Initial setup position of the robot.

### 7. Usage

The following chapter will introduce the reader to the usage of the robot. Starting with a Overview of the robot’s setup. Then an explanation on how to charge the robot followed by how to connect to the robot and how to control it.

### 7.1 Overview

Figure 36 shows an overview of the robot’s control system. As can be seen, there are three main UART lines that daisy chain the servos into left, right and spine motors. Nose and head touch sensors are directly connected to the spine adapter board, the cameras are connected to the raspberry pi via a USB hub. All other sensors are connected via the servos. The Battery is directly connected to the Spine Adapter board. The spine Adapter also carries an IMU additionally to the charging electronics and the power regulators. The connection between the Spine adapter and the Raspberry Pi is also done via UART.

Fig. 36. Electrical setup of the robot.

### 7.2 Charging

The robot can be charged via the wireless charging coil as shown in Figure 37 on the bottom using any QI-standard charging platform. The charging can be done with the robot switched on or off. As the wireless charger on the robot does not balance the LiPo battery, it is recommended to charge the battery directly with a standard LiPo charger for 2 celled batteries.

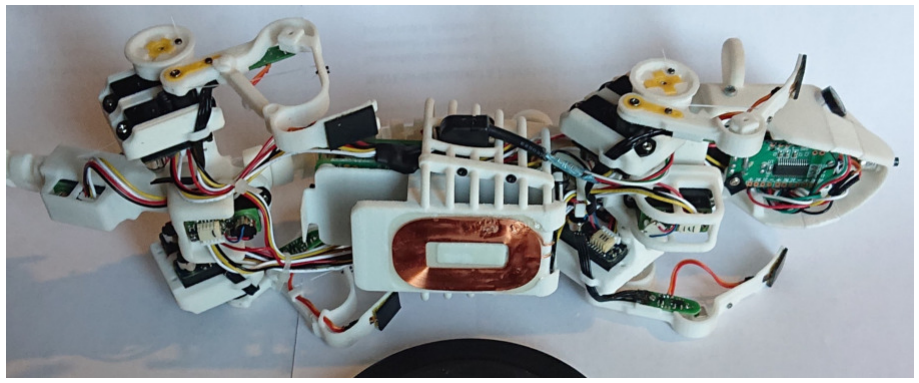
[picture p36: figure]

Fig. 37. charging coil of the robot.

### 7.3 Communication

When everything is set up, you can communicate with the servos or the spine adapter board from the Raspberry Pi using minicom https://help.ubuntu.com/community/Minicom. The settings are as shown in subsection 6.1. To view the programming possibilities on the spine type ”:??” and you will prompted by a function overview. To talk to one of the servos you will have to know the UART line and the ID of the servo. The UART lines are ”0” for the left side, ”1” for the right side and ”2” for the center line motors including the head. The motor IDs go from 0-3 for the left and right side and 0-4 for the centre line. So calling the info promt for the head motor would be ”:24??”. The IDs are listed in detail in Table 5.

Line | ID | Servo
0
| 00 | Right Hind Coil
| 01 | Right Hind Leg
| 02 | Right Fore Coil
| 03 | Right Fore Leg
1
| 10 | Left Hind Coil
| 11 | Left Hind Leg
| 12 | Left Fore Coil
| 13 | Left Fore Leg
2
| 20 | Flex Spine
| 21 | Lateral Flex Spine
| 22 | Tail
| 23 | Neck Servo
| 24 | Head Servo

Table 5. Servo IDs on the robot.

### 7.4 Control

You can start the control software form the github with ”./SimpleMaus”. You will be presented with the following greeting:

*****************************************
Welcome t o t h e NRP Mouse C o n t r o l S o ft w a r e
***************************************** You ha ve t h e f o l l o w i n g O pti o n s :

C o n t r o l:−−−−−−−−−−−−−−−−−−−−−−−−−−
s : St o p M ot o r s
h : Hold p r o g ram
q : Q uit p r o g ram
+: I n c r e a s e Speed
−: D e c r e a s e Speed

Walking:−−−−−−−−−−−−−−−−−−−−−−−−−−
i : I n i t i a l i z e p o s e
w: Walk f o r w a r d T r o t t
a : Walk r i g h t t h e more t h e o f t e n you p r e s s d : Walk l e f t t h e more t h e o f t e n you p r e s s b : Walk f o r w a r d Bound
n : Walk f o r w a r d Bound2

S i t t i n g:−−−−−−−−−−−−−−−−−−−−−−−−−−
y : S i t up
f : P r e s s b ot h paws up
t : L i f t b ot h paws up
e : L i f t l e f t paw
r : L i f t r i g h t paw
x : S i t down

F i l e s:−−−−−−−−−−−−−−−−−−−−−−−−−−−−
o : Read m oti o n d a t a f rom m oti o n . t x t l : Pl a y b a c k d a t a o nce
k : Pl a y b a c k d a t a r e p e a t e d l y
p : P r i n t p o s i t i o n d a t a t o f i l e

As you can see the options are separated into Control, Walking, Sitting and Files. For control:
”s” disables the motors by deactivating H-Bridge on the Motor PCB. ”h” holds the program immediately. ”q” quits the program and returns to the terminal. For walking:
”i” sets the robot to it’s initial pose. ”w” sets the robot to a forward walking motion. ”a/d” activate the lateral flex servo in the spine to move the robot left or right. The Bounding gaits are experimental. For Sitting:
The sitting pose is experimental and the robot can not sit up by itself. after pushing ”y” it can be manually brought into a sitting position. from there the paws can be moved according to the remaining options. Files:
Motion files can be read and played back on the robot. To read a motion file it has to be called ”motion.txt” and located in a sub folder ”motions” as is in the git repository. ”o” reads the data from the file. ”l” plays the file once, ”k” plays the file in an infinite loop. ”p” saves to data from the last motion into a file.

Acknowledgments

Thanks to everyone who helped with this project.

Publications

The following publications have been published about the different NeRmo robots [1], [2], [3].

[1] Lucas P, Florian Walter AK (2018) Design of a biomimetic rodent robot (Technische Universitaet Muenchen, Institut fuer Informatik), TUM-I1873. https://doi.org/10.14459/2018md1464578
[2] Lucas P, Oota S, Conradt J, Knoll A (2019) Development of the neurorobotic mouse. Proceedings IEEE International Conference on Cyborgs and Bionic Systems (Munich, Germany), , p 6.
[3] Lucas P, Morin FO, Conradt J, Knoll A (2020) Neurorobotic mouse (nermo) v4.1 (Technische Universitaet Muenchen, Institut fuer Informatik), TUM-I2081. https://doi.org/10.14459/2020md1540519

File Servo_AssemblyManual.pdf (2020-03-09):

This File is part of the Nermo User Manual

peer.lucas@tum.de

## Servo Assembly Manual

Parts needed:
- PowerHD HD-DSM44
- M1x12 (2 pieces)
- ServoBoard-Rev4
- Magnet 2x2x2 mm
- Servo magnet holder (3D Print)
1. Unscrew the back of the Servo and remove it

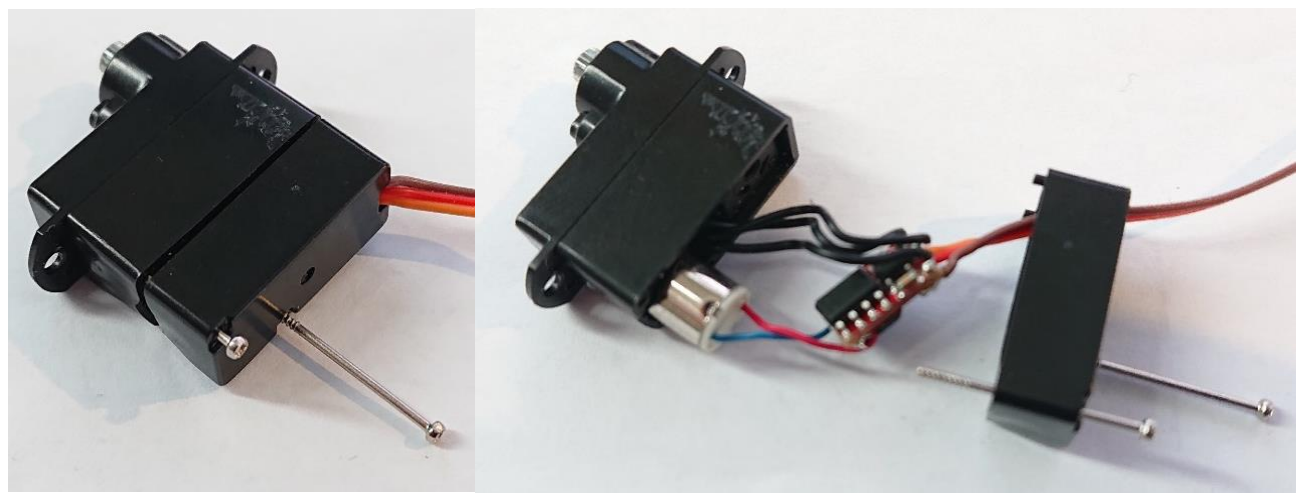
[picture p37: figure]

2. Carefully remove the Potentiometer

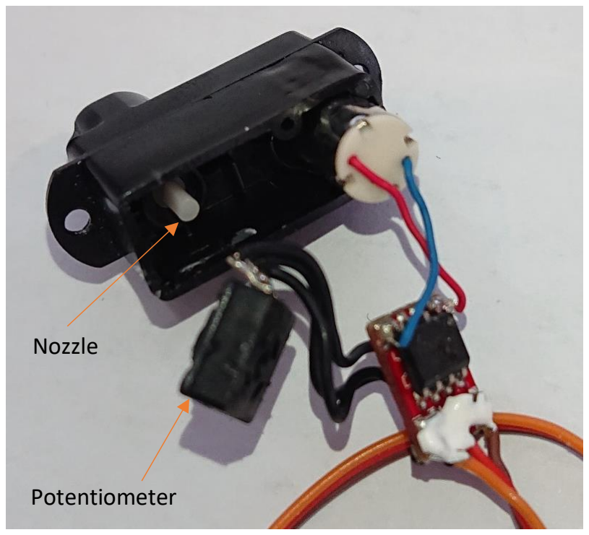
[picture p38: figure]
Nozzle; Potentiometer
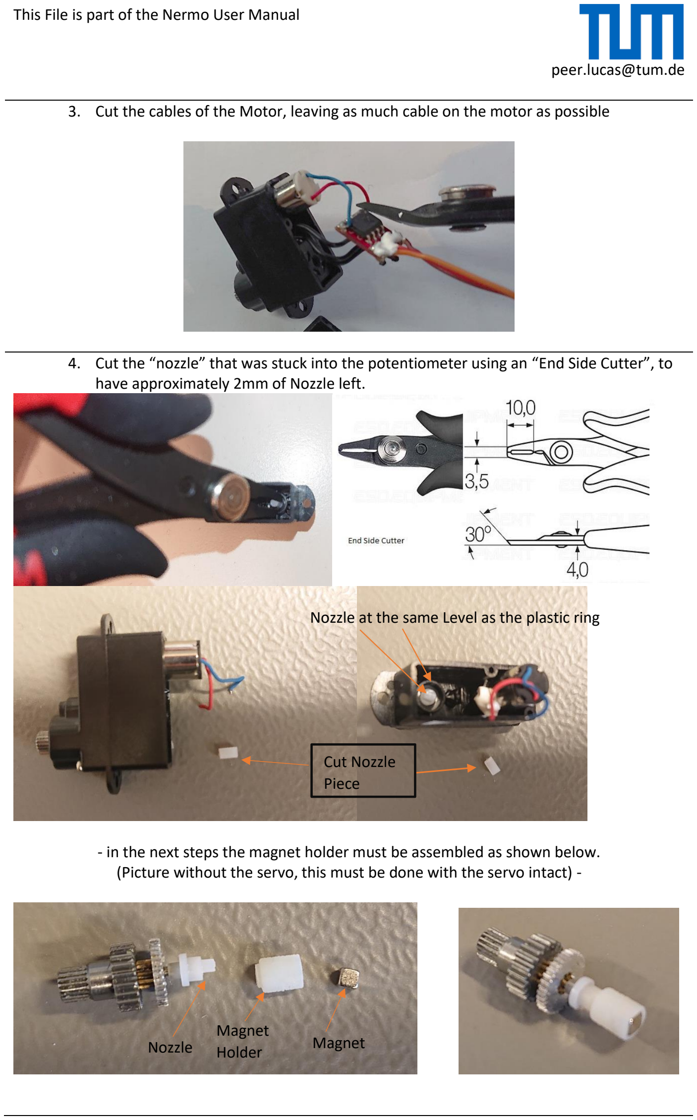
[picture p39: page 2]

peer.lucas@tum.de

3. Cut the cables of the Motor, leaving as much cable on the motor as possible
4. Cut the “nozzle” that was stuck into the potentiometer using an “End Side Cutter”, to have approximately 2mm of Nozzle left.
- in the next steps the magnet holder must be assembled as shown below. (Picture without the servo, this must be done with the servo intact) -

Cut Nozzle
Piece
Nozzle | Magnet

Magnet
Holder

Nozzle at the same Level as the plastic ring

peer.lucas@tum.de

5. Insert a little bit GEL instant glue into the D-Shaped end of the magnet holder and push it onto the nozzle.
(NO liquid glue, this might glue the gears in place)

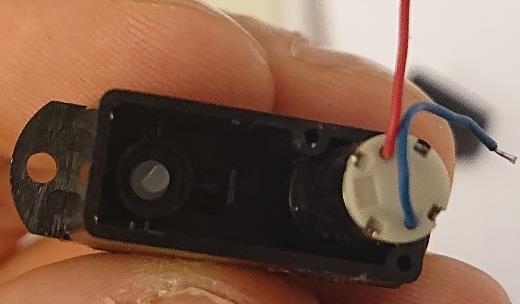
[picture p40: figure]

6. Determine the polarization of the Magnet.

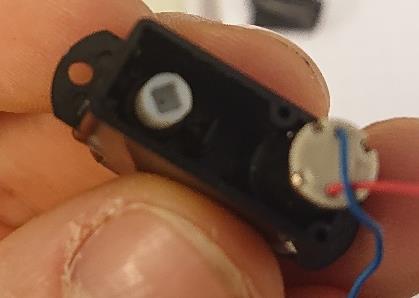
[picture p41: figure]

For the Servo to work, both positive and negative side (i.e. the pole separation line) of the magnet need to be facing outside of the magnet holder.
To determine the polarization, you can use a bigger magnet with known polarization. If the smaller magnet is centred on the bigger magnet, it should have the correct orientation, if it is of to the side it just faces one pole outside.

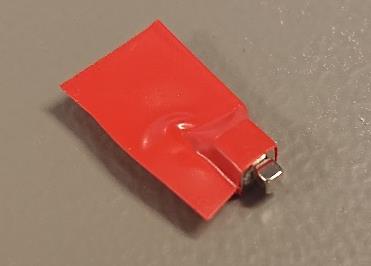
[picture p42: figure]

7. With this orientation set, you can glue the magnet into the magnet holder. Make sure, that the whole assembly stays below approximately two millimetres below the servo housing.

Outside facing side of the magnet.
+ | -

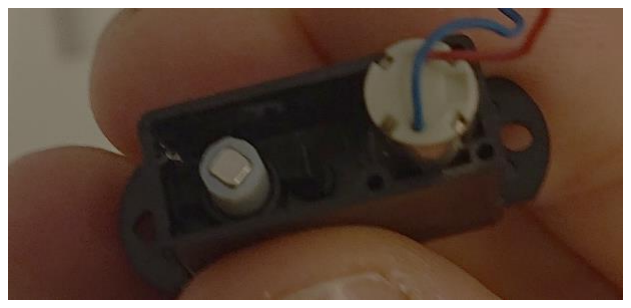
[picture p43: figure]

peer.lucas@tum.de

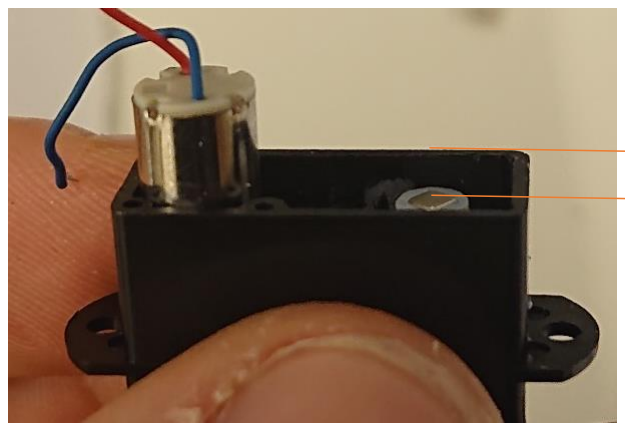
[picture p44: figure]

8. Remove the top left screw from the top of the servo

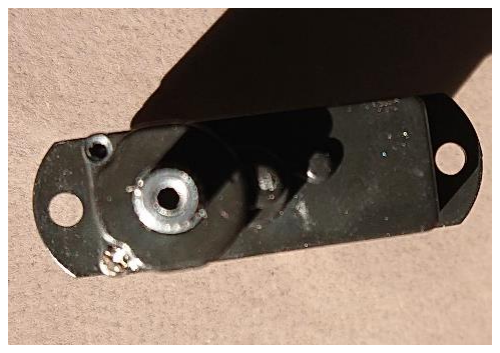
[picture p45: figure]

9. Attach the Servo PCB to the Servo and screw it in place

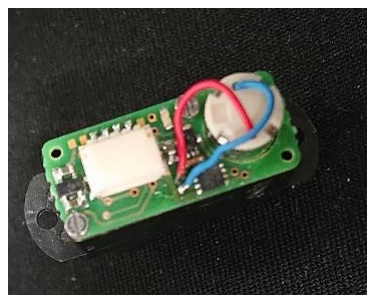
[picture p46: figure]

10. Solder the Motor Cables to the respective pads on the motor. (WATCH OUT FOR CORRECT COLOURS)

>= 2mm

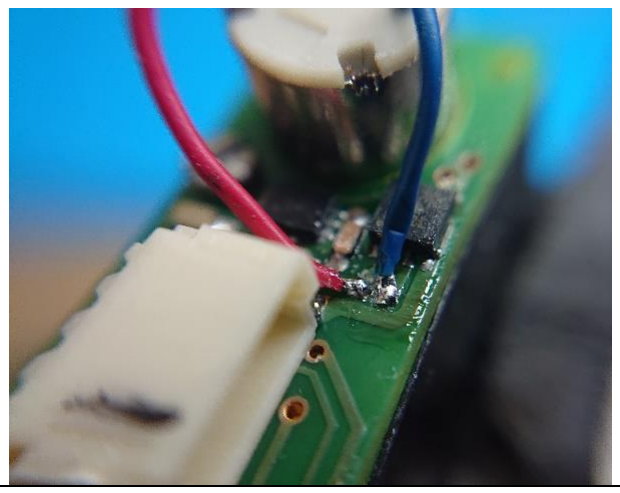
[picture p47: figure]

peer.lucas@tum.de

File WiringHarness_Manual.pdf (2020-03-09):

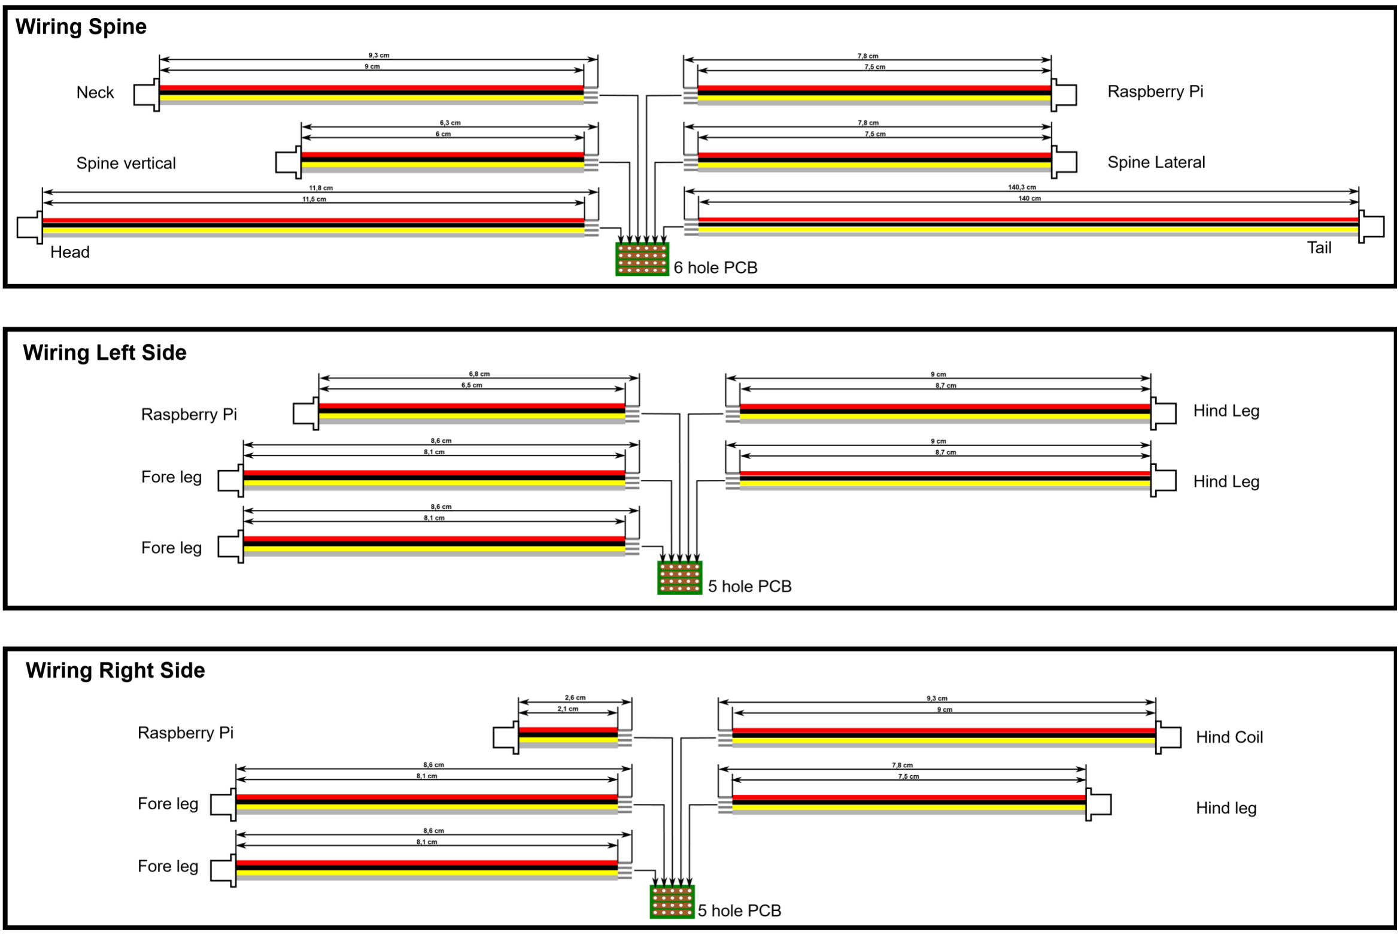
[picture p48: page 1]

Please make sure to avoid any wires coming up above the PCB but have a clean surface so all short circuits are avoided.

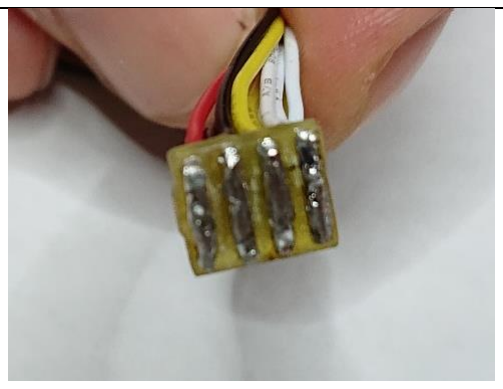
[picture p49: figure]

The same avoidance of short circuits is to be done with the bottom of the PCB.

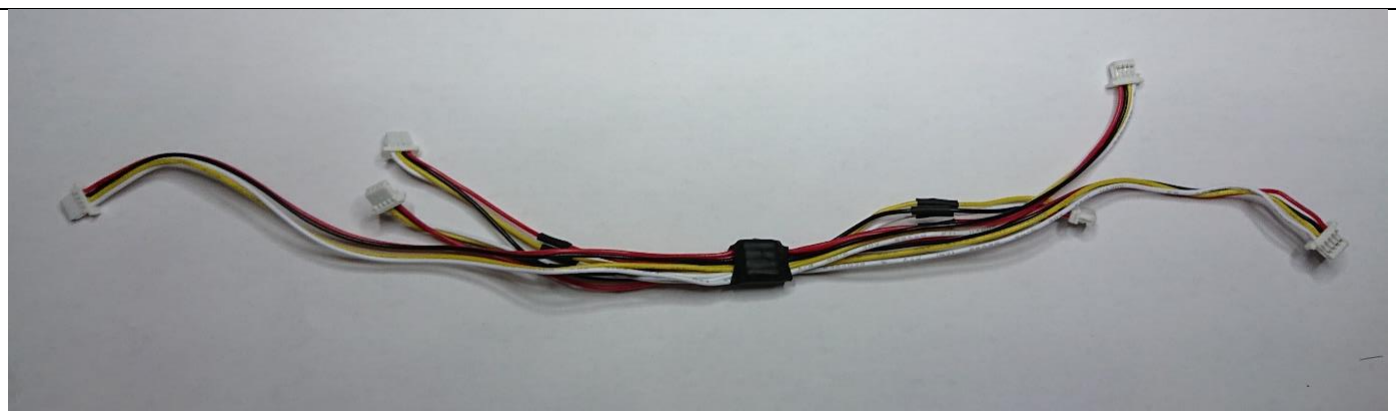
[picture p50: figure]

Finally, cover the PCB with shrink-wrap

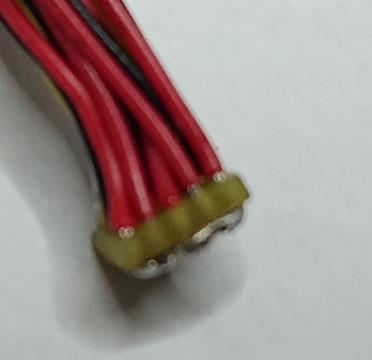
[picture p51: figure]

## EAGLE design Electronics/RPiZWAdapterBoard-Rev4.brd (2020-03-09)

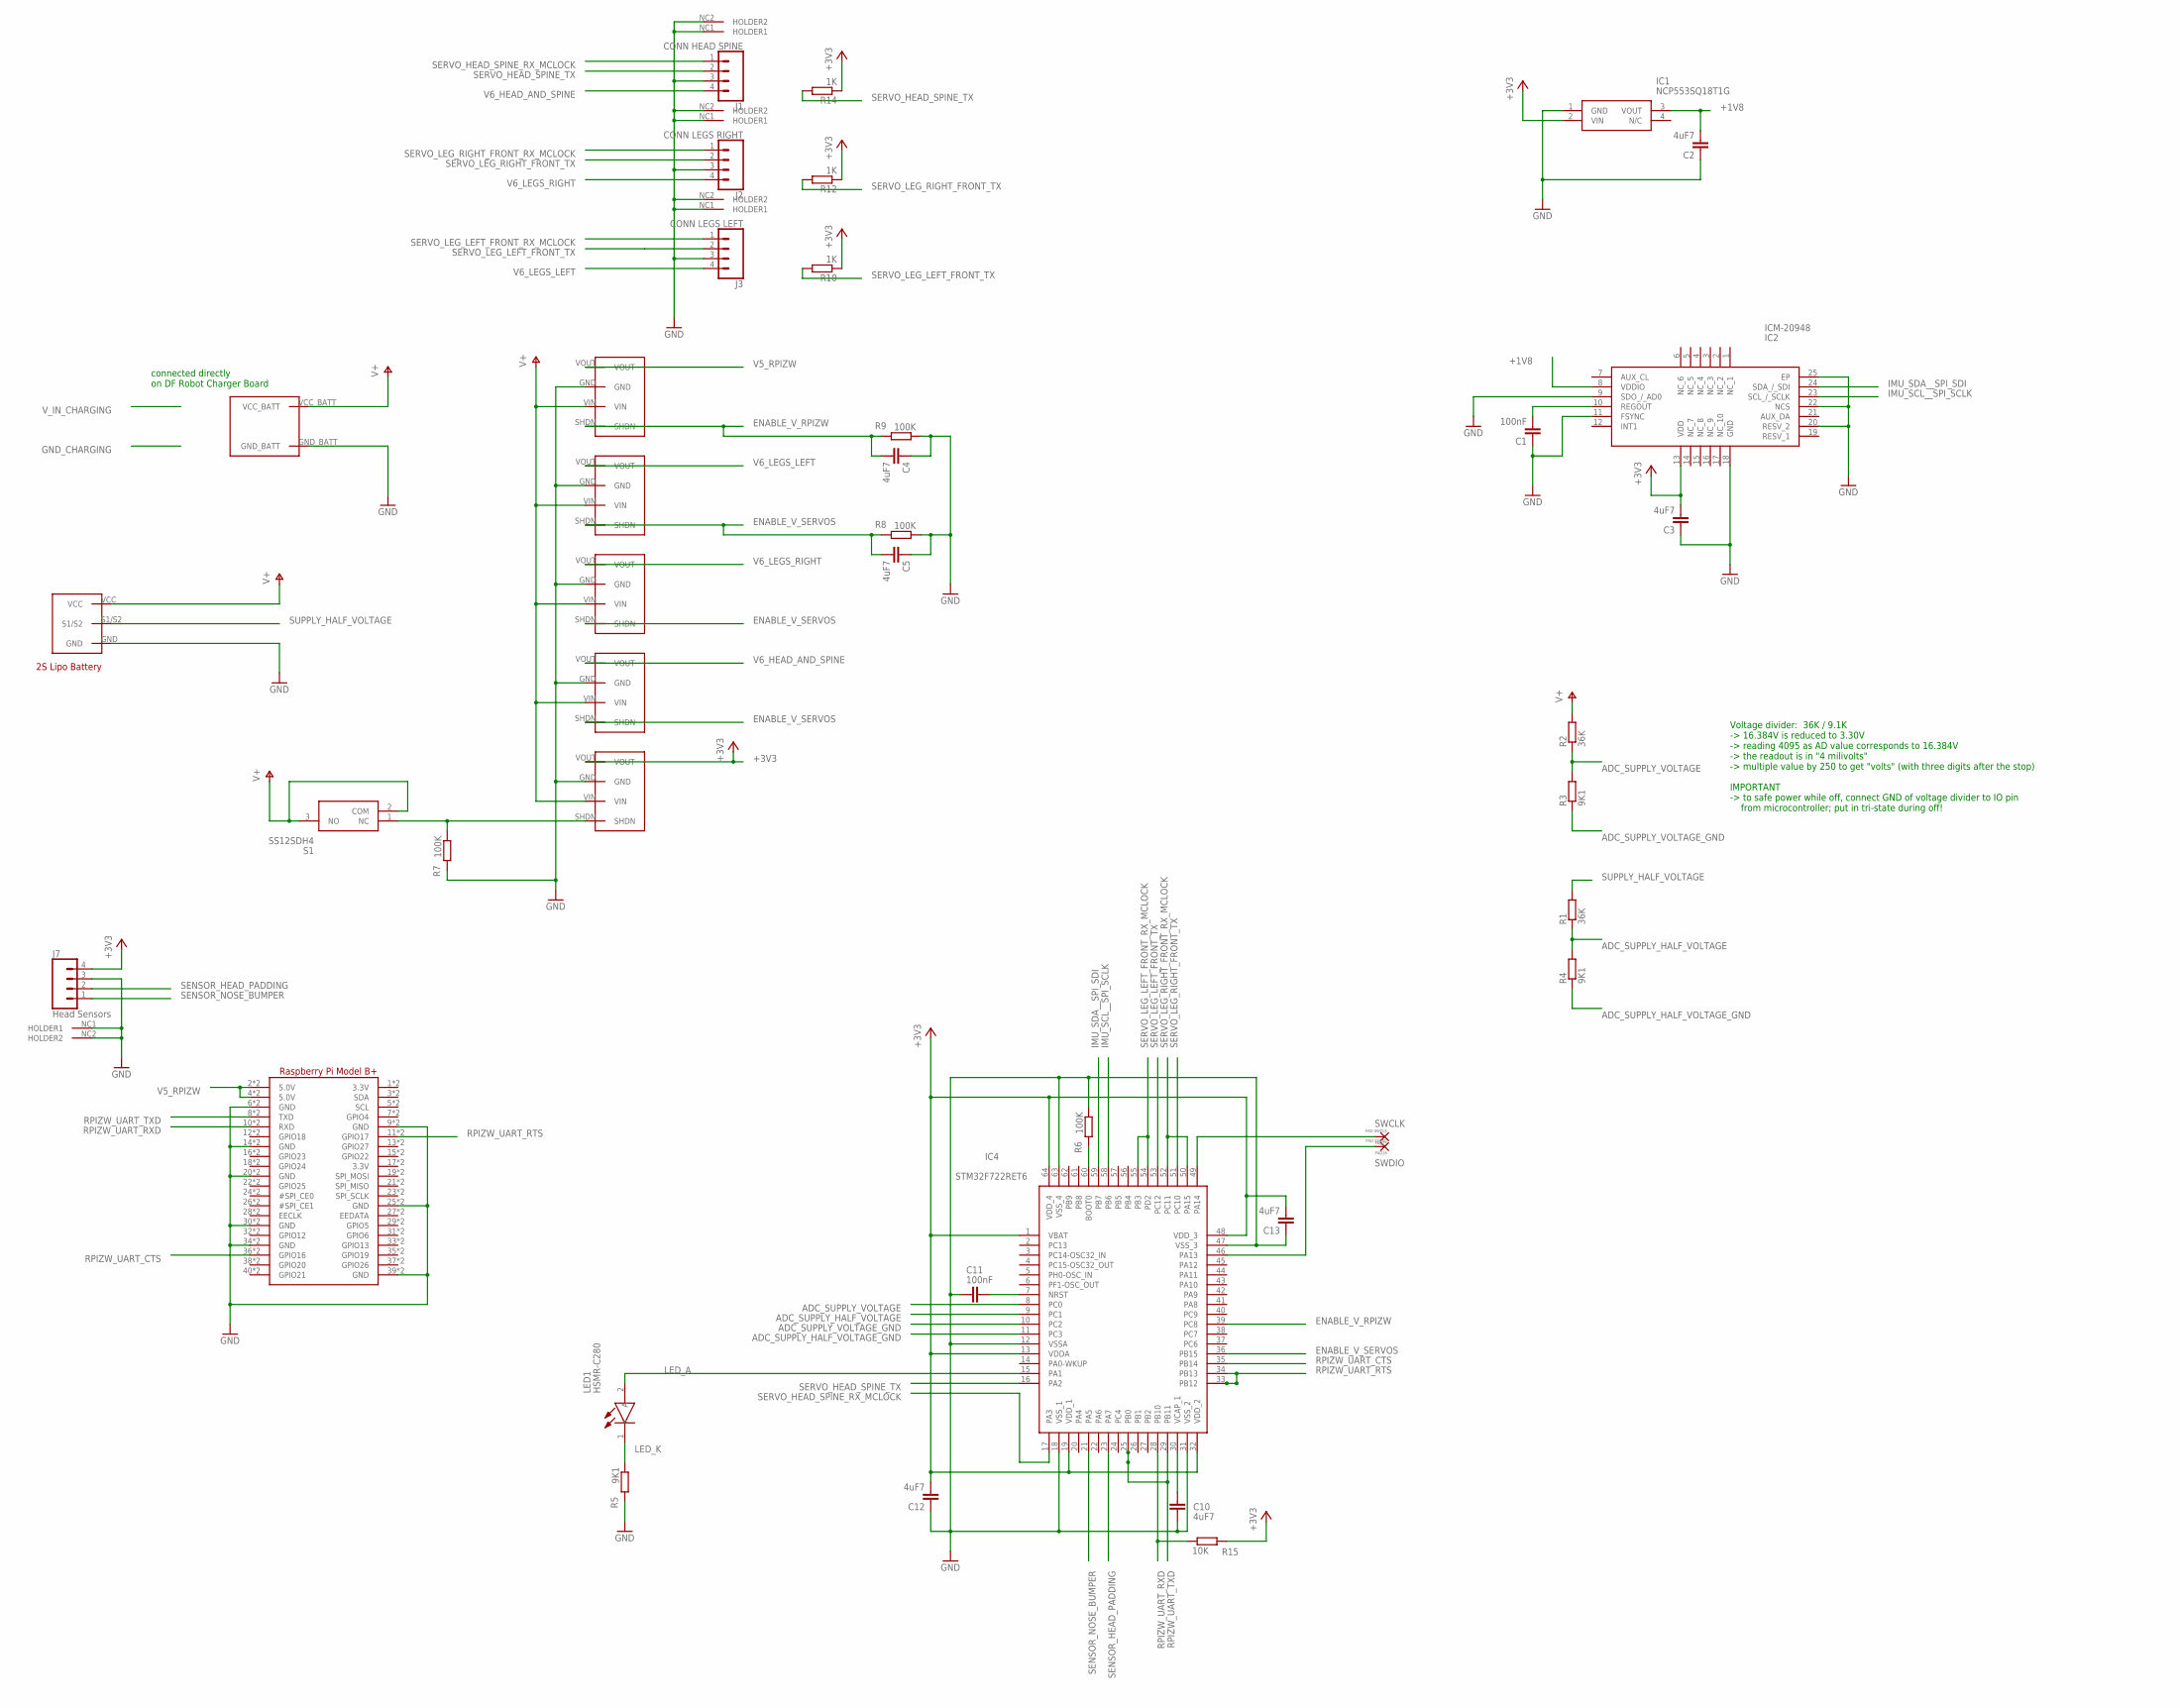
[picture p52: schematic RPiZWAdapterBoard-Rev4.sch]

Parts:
C1, C11: 100nF; C0402
C2, C3, C4, C5, C10, C12, C13: 4uF7; C0402
IC1: NCP553SQ18T1G; NCP563SQ18T1G
IC2: ICM-20948; QFN40P300X300X105-25N
IC4: STM32F722RET6; QFP50P1200X1200X160-64N
J1: CONN HEAD SPINE; JST04_SH_1MM
J2: CONN LEGS RIGHT; JST04_SH_1MM
J3: CONN LEGS LEFT; JST04_SH_1MM
J7: Head Sensors; JST04_SH_1MM
LED1: HSMR-C280; LEDC1005X50N
PAD25: PAD SWCLK; SMD12X08
PAD26: PAD SWDIO; SMD12X08
R1, R2: 36K; R0402
R3, R4, R5: 9K1; R0402
R6, R7, R8, R9: 100K; R0402
R10, R12, R14: 1K; R0402
R15: 10K; R0402
RPI1: MICROBUILDER_RASPBERRYPI_BPLUSWIDE; MICROBUILDER_PI_BONNET_THMSMT_WIDE
S1: SS12SDH4
U$1, U$3, U$4, U$5, U$6: POLOLU_REGULATOR
U$7: JST-S3B-XH-A_BATTCON; JST-S3B-XH-A
U$8: DFROBOT_CHARGER_CUTOUTNARROW; DFROBOT_CHARGER_CUTOUT_NARROW

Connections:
+1V8: C2.2, IC1.3 (VOUT), IC2.8 (VDDIO)
+3V3: C3.2, C12.2, C13.2, IC1.2 (VIN), IC2.13 (VDD), IC4.1 (VBAT), IC4.13 (VDDA), IC4.19 (VDD_1), IC4.32 (VDD_2), IC4.48 (VDD_3), IC4.64 (VDD_4), J7.4, R10.1, R12.1, R14.1, R15.2, U$6.VOUT
ADC_SUPPLY_HALF_VOLTAGE: IC4.9 (PC1), R1.1, R4.2
ADC_SUPPLY_HALF_VOLTAGE_GND: IC4.11 (PC3), R4.1
ADC_SUPPLY_VOLTAGE: IC4.8 (PC0), R2.1, R3.2
ADC_SUPPLY_VOLTAGE_GND: IC4.10 (PC2), R3.1
ENABLE_V_RPIZW: C4.2, IC4.39 (PC8), R9.2, U$1.SHDN
ENABLE_V_SERVOS: C5.2, IC4.36 (PB15), R8.2, U$3.SHDN, U$4.SHDN, U$5.SHDN
GND: C1.1, C2.1, C3.1, C4.1, C5.1, C10.1, C11.2, C12.1, C13.1, IC1.1 (GND), IC2.9 (SDO_/_AD0), IC2.11 (FSYNC), IC2.18 (GND), IC2.20 (RESV_2), IC2.22 (NCS), IC2.25 (EP), IC4.12 (VSSA), IC4.18 (VSS_1), IC4.31 (VSS_2), IC4.47 (VSS_3), IC4.63 (VSS_4), J1.3, J1.NC1 (HOLDER1), J1.NC2 (HOLDER2), J2.3, J2.NC1 (HOLDER1), J2.NC2 (HOLDER2), J3.3, J3.NC1 (HOLDER1), J3.NC2 (HOLDER2), J7.3, J7.NC1 (HOLDER1), J7.NC2 (HOLDER2), R5.2, R6.1, R7.2, R8.1, R9.1, RPI1.6 (GND), RPI1.9 (GND), RPI1.14 (GND), RPI1.20 (GND), RPI1.25 (GND), RPI1.30 (GND), RPI1.34 (GND), RPI1.39 (GND), RPI1.S6 (GND), RPI1.S9 (GND), RPI1.S14 (GND), RPI1.S20 (GND), RPI1.S25 (GND), RPI1.S30 (GND), RPI1.S34 (GND), RPI1.S39 (GND), U$1.GND, U$3.GND, U$4.GND, U$5.GND, U$6.GND, U$7.GND, U$8.GND_BATT
IMU_SCL__SPI_SCLK: IC2.23 (SCL_/_SCLK), IC4.58 (PB6)
IMU_SDA__SPI_SDI: IC2.24 (SDA_/_SDI), IC4.59 (PB7)
LED_A: IC4.15 (PA1), LED1.2 (A)
LED_K: LED1.1 (K), R5.1
unnamed: R7.1, S1.1 (NC), U$6.SHDN
unnamed: C1.2, IC2.10 (REGOUT)
unnamed: IC4.60 (BOOT0), R6.2
unnamed: C11.1, IC4.7 (NRST)
unnamed: C10.2, IC4.30 (VCAP_1)
RPIZW_UART_CTS: IC4.35 (PB14), RPI1.36 (GPIO16), RPI1.S36 (GPIO16)
RPIZW_UART_RTS: IC4.33 (PB12), IC4.34 (PB13), RPI1.11 (GPIO17), RPI1.S11 (GPIO17)
RPIZW_UART_RXD: IC4.28 (PB10), R15.1, RPI1.10 (RXD), RPI1.S10 (RXD)
RPIZW_UART_TXD: IC4.25 (PB0), IC4.29 (PB11), RPI1.8 (TXD), RPI1.S8 (TXD)
SENSOR_HEAD_PADDING: IC4.23 (PA7), J7.2
SENSOR_NOSE_BUMPER: IC4.21 (PA5), J7.1
SERVO_HEAD_SPINE_RX_MCLOCK: IC4.17 (PA3), J1.1
SERVO_HEAD_SPINE_TX: IC4.16 (PA2), J1.2, R14.2
SERVO_LEG_LEFT_FRONT_RX_MCLOCK: IC4.54 (PD2), IC4.55 (PB3), J3.1
SERVO_LEG_LEFT_FRONT_TX: IC4.53 (PC12), J3.2, R10.2
SERVO_LEG_RIGHT_FRONT_RX_MCLOCK: IC4.50 (PA15), IC4.52 (PC11), J2.1
SERVO_LEG_RIGHT_FRONT_TX: IC4.51 (PC10), J2.2, R12.2
SUPPLY_HALF_VOLTAGE: R1.2, U$7.S1/S2
SWCLK: IC4.49 (PA14), PAD25.1
SWDIO: IC4.46 (PA13), PAD26.1
V5_RPIZW: RPI1.2 (5.0V), RPI1.4 (5.0V), RPI1.S2 (5.0V), RPI1.S4 (5.0V), U$1.VOUT
V6_HEAD_AND_SPINE: J1.4, U$5.VOUT
V6_LEGS_LEFT: J3.4, U$3.VOUT
V6_LEGS_RIGHT: J2.4, U$4.VOUT
V+: R2.2, S1.2 (COM), S1.3 (NO), U$1.VIN, U$3.VIN, U$4.VIN, U$5.VIN, U$6.VIN, U$7.VCC, U$8.VCC_BATT

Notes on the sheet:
Voltage divider: 36K / 9.1K -> 16.384V is reduced to 3.30V -> reading 4095 as AD value corresponds to 16.384V -> the readout is in "4 milivolts" -> multiple value by 250 to get "volts" (with three digits after the stop) IMPORTANT -> to safe power while off, connect GND of voltage divider to IO pin 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
connected directly on DF Robot Charger Board

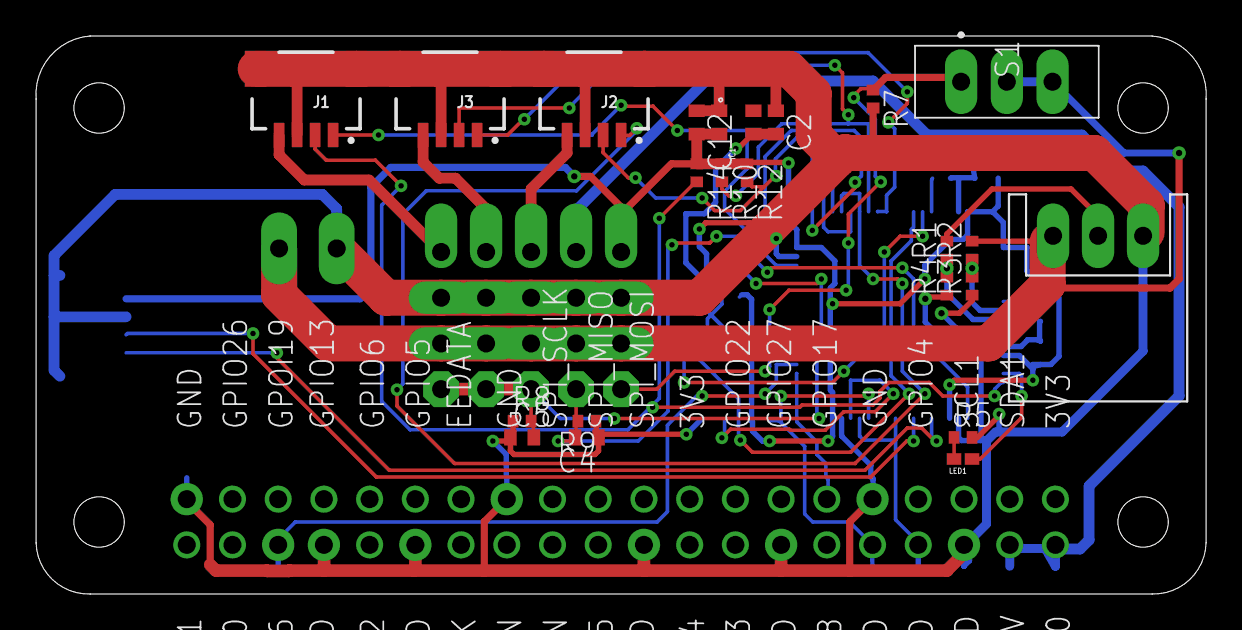
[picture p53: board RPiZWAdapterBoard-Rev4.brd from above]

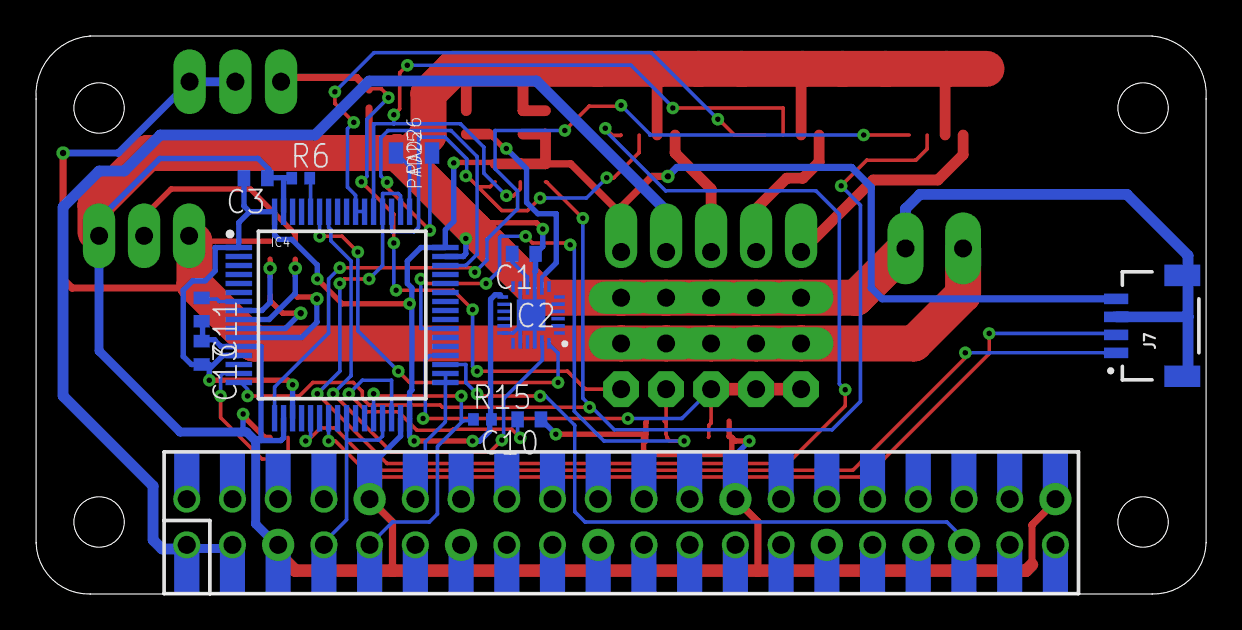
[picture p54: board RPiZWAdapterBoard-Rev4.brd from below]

Board: 2 copper layers, 65.0 x 31.0 mm, 41 parts (14 on the bottom side), 38 nets.

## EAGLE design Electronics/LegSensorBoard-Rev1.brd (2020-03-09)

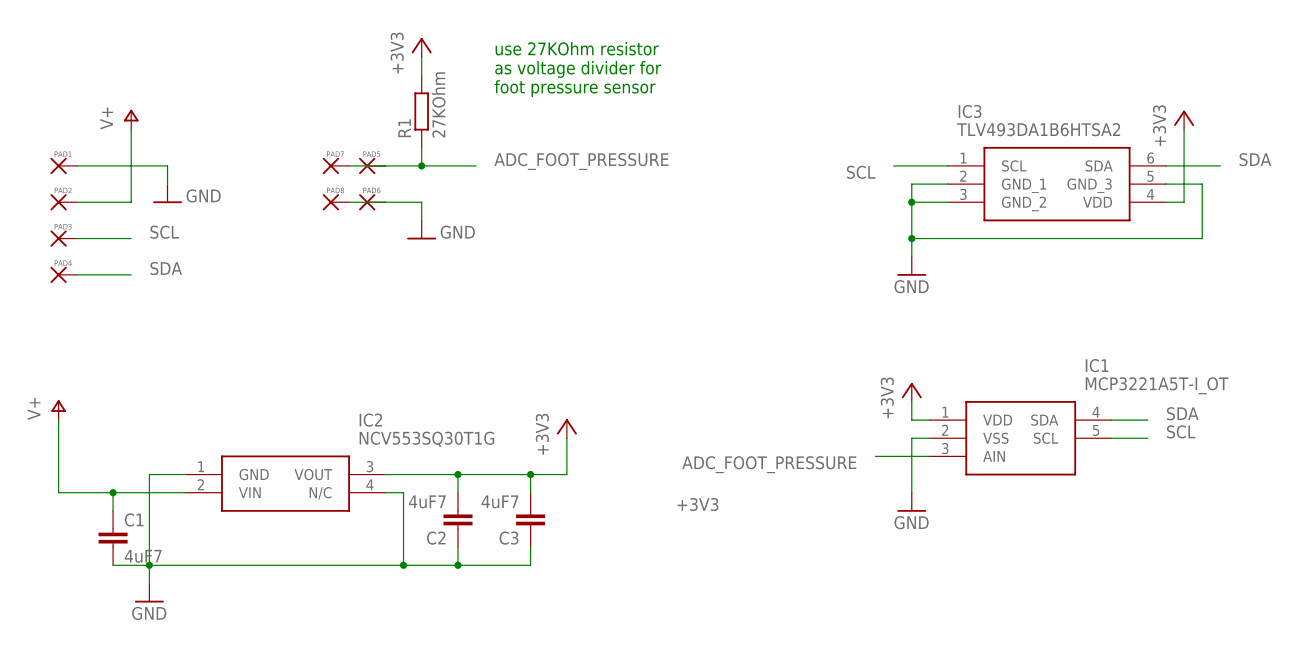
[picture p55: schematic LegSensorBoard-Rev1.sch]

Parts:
C1, C2, C3: 4uF7; C0402
IC1: MCP3221A5T-I_OT; SOT95P270X145-5N
IC2: NCV553SQ30T1G; NCP563SQ18T1G
IC3: TLV493DA1B6HTSA2; SOT95P250X110-6N
PAD1, PAD2, PAD3, PAD4: SMD-PAD20X07; SMD20X07
PAD5, PAD6, PAD7, PAD8: SMD-PAD14X08; SMD14X08
R1: 27KOhm; R0402

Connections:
+3V3: C2.2, C3.2, IC1.1 (VDD), IC2.3 (VOUT), IC3.4 (VDD), R1.2
ADC_FOOT_PRESSURE: IC1.3 (AIN), PAD5.1, PAD7.1, R1.1
GND: C1.2, C2.1, C3.1, IC1.2 (VSS), IC2.1 (GND), IC2.4 (N/C), IC3.2 (GND_1), IC3.3 (GND_2), IC3.5 (GND_3), PAD1.1, PAD6.1, PAD8.1
SCL: IC1.5 (SCL), IC3.1 (SCL), PAD3.1
SDA: IC1.4 (SDA), IC3.6 (SDA), PAD4.1
V+: C1.1, IC2.2 (VIN), PAD2.1

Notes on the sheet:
use 27KOhm resistor as voltage divider for foot pressure sensor

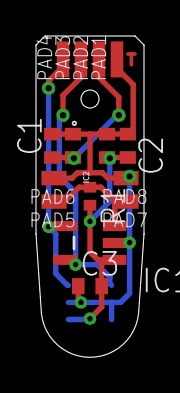
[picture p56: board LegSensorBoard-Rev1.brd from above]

Board: 2 copper layers, 6.0 x 17.8 mm, 15 parts (1 on the bottom side), 6 nets.

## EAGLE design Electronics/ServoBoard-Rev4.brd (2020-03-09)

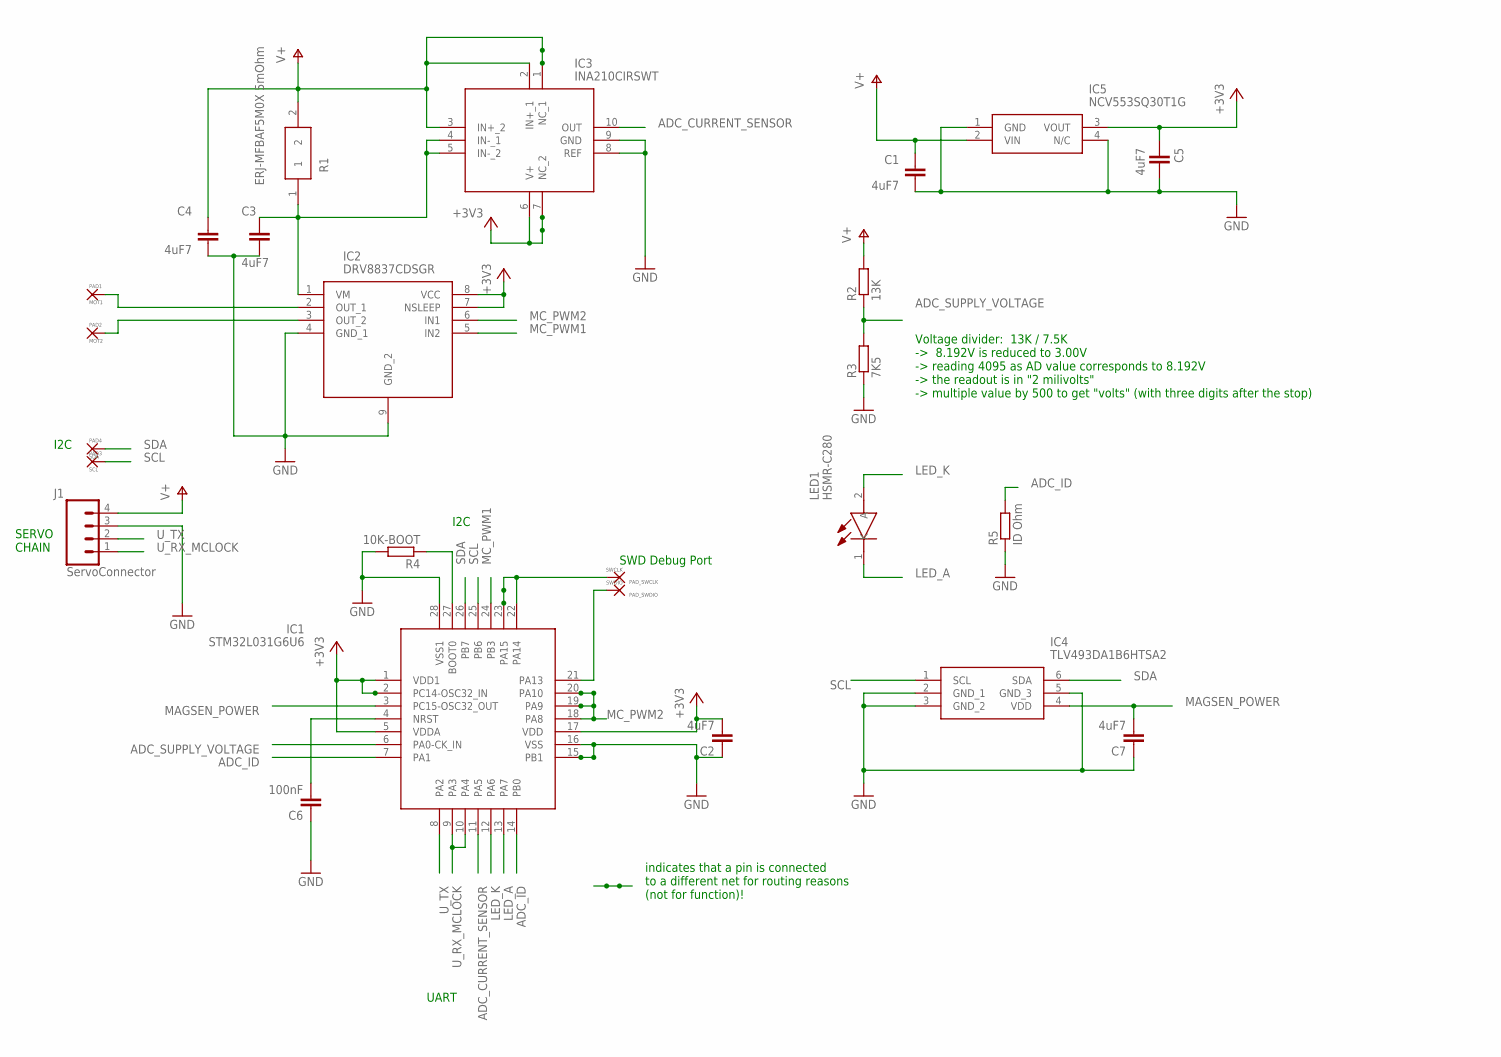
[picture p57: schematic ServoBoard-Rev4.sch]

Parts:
C1, C2, C3, C4, C5, C7: 4uF7; C0402
C6: 100nF; C0201
IC1: STM32L031G6U6; QFN50P400X400X60-28N
IC2: DRV8837CDSGR; SON50P200X200X80-9N
IC3: INA210CIRSWT; QFN40P140X180X55-10N
IC4: TLV493DA1B6HTSA2; SOT95P250X110-6N
IC5: NCV553SQ30T1G; NCP563SQ18T1G
J1: ServoConnector; JST04_SH_1MM
LED1: HSMR-C280; LEDC1005X50N
PAD1: MOT1; SMD12X07
PAD2: MOT2; SMD12X07
PAD3: SCL; SMD14X06
PAD4: SDA; SMD14X06
PAD_SWCLK: SWCLK; SMD06X06
PAD_SWDIO: SWDIO; SMD06X06
R1: ERJ-MFBAF5M0X 5mOhm; RESM106X40N
R2: 13K; R0402
R3: 7K5; R0402
R4: 10K-BOOT; R0402
R5: ID Ohm; R0402

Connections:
+3V3: C2.2, C5.1, IC1.1 (VDD1), IC1.2 (PC14-OSC32_IN), IC1.5 (VDDA), IC1.17 (VDD), IC2.7 (NSLEEP), IC2.8 (VCC), IC3.6 (V+), IC3.7 (NC_2), IC5.3 (VOUT)
ADC_CURRENT_SENSOR: IC1.11 (PA5), IC3.10 (OUT)
ADC_ID: IC1.7 (PA1), IC1.14 (PB0), R5.2
ADC_SUPPLY_VOLTAGE: IC1.6 (PA0-CK_IN), R2.1, R3.2
BOOT0: IC1.27 (BOOT0), R4.1
GND: C1.2, C2.1, C3.2, C4.2, C5.2, C6.1, C7.1, IC1.15 (PB1), IC1.16 (VSS), IC1.28 (VSS1), IC2.4 (GND_1), IC2.9 (GND_2), IC3.8 (REF), IC3.9 (GND), IC4.2 (GND_1), IC4.3 (GND_2), IC4.5 (GND_3), IC5.1 (GND), IC5.4 (N/C), J1.3, R3.1, R4.2, R5.1
LED_A: IC1.13 (PA7), LED1.1 (K)
LED_K: IC1.12 (PA6), LED1.2 (A)
MAGSEN_POWER: C7.2, IC1.3 (PC15-OSC32_OUT), IC4.4 (VDD)
MC_PWM1: IC1.24 (PB3), IC2.5 (IN2)
MC_PWM2: IC1.18 (PA8), IC1.19 (PA9), IC1.20 (PA10), IC2.6 (IN1)
MOTOR_1: IC2.2 (OUT_1), PAD1.1
MOTOR_2: IC2.3 (OUT_2), PAD2.1
NRST: C6.2, IC1.4 (NRST)
SCL: IC1.25 (PB6), IC4.1 (SCL), PAD3.1
SDA: IC1.26 (PB7), IC4.6 (SDA), PAD4.1
SWCLK: IC1.22 (PA14), IC1.23 (PA15), PAD_SWCLK.1
SWDIO: IC1.21 (PA13), PAD_SWDIO.1
U_RX_MCLOCK: IC1.9 (PA3), IC1.10 (PA4), J1.1
U_TX: IC1.8 (PA2), J1.2
V+: C1.1, C4.1, IC3.1 (NC_1), IC3.2 (IN+_1), IC3.3 (IN+_2), IC5.2 (VIN), J1.4, R1.2, R2.2
V_SENSOR: C3.1, IC2.1 (VM), IC3.4 (IN-_1), IC3.5 (IN-_2), R1.1

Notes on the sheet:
Voltage divider: 13K / 7.5K -> 8.192V is reduced to 3.00V -> reading 4095 as AD value corresponds to 8.192V -> the readout is in "2 milivolts" -> multiple value by 500 to get "volts" (with three digits after the stop)
SWD Debug Port
I2C
UART
SERVO CHAIN
indicates that a pin is connected to a different net for routing reasons (not for function)!

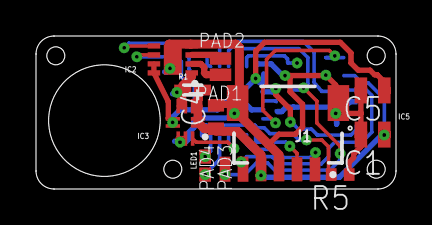
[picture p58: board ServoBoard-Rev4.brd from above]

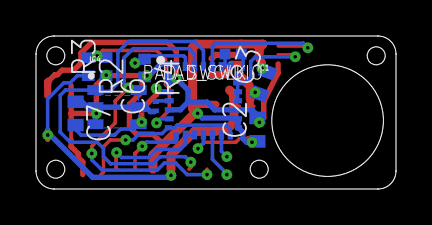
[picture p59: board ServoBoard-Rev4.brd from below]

Board: 2 copper layers, 20.0 x 8.5 mm, 25 parts (11 on the bottom side), 22 nets.

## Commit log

2020-03-02 STL Files inserted and renamed
    [Body_Coil - Copy.stl, Body_Coil.stl, Body_Elektronics_mount.stl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]
2020-03-05 Updated names; included User Manual
    User manual in its first stage, only asembly instructions
    [Body_Solarplexus.stl]
2020-03-09 Manual extended, Added Electronics
    Added Leg module soldering to Manual
    Added Setup to Manual
    Added electronics files
    [LegSensorBoard-Rev1.brd, LegSensorBoard-Rev1.sch, RPiZWAdapterBoard-Rev4.brd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]
2020-03-09 updated folders and structure
    [Body_Coil - Copy.stl, Body_Coil.stl, Body_Solarplexus.stl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]
2020-03-09 updated Manuals
    [Magnet_holder.stl]
